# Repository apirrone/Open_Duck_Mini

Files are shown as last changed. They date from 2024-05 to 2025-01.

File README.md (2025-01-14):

# Open Duck Mini v2

Capture d’écran du 2025-01-14 15-44-05

I'm making a miniature version of the BDX Droid by Disney. It is about 42 centimeters tall with its legs extended.
The full BOM cost should be under $400 !

# This repo

This is kind of a hub where I centralize all resources related to this project. This is a working repo, so there are a lot of undocumented scripts :) I'll try to clean things up at some point.

# CAD

https://cad.onshape.com/documents/64074dfcfa379b37d8a47762/w/3650ab4221e215a4f65eb7fe/e/0505c262d882183a25049d05

See [this document](docs/prepare_robot.md) for getting from a onshape design to a simulated robot in MuJoCo

# RL stuff

We now use [AWD](https://github.com/rimim/AWD)

## Actuator identification 

We used Rhoban's [BAM](https://github.com/Rhoban/bam)

# BOM

> The BOM is not yet fully finalized, wait a bit before ordering stuff

https://docs.google.com/spreadsheets/d/1gq4iWWHEJVgAA_eemkTEsshXqrYlFxXAPwO515KpCJc/edit?usp=sharing

# Build Guide

## Print Guide

TODO

## Assembly Guide
TODO

TODO

# Embedded runtime

This repo contains the code to run the policies on the onboard computer (Raspberry pi zero 2w) https://github.com/apirrone/Open_Duck_Mini_Runtime

> Thanks a lot to HuggingFace and Pollen Robotics for sponsoring this project !

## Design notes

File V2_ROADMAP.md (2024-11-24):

# V2 ROADMAP

First make the placo walk work with foot sensors -> This validate the design, the motors are powerful enough and urdf is close to the real thing

## CAD

### Notes :
- Plan mounting holes for aesthetic stuff later ?
- Plan to hide the cables somehow
- Integrate feet contact sensors (switchs, not fsr I think)

### TODO
  - [] Full redesign using feetech motors.
    - [] Select the motors STS3215 or STS3250 ? 5v ? 12 v (if 12v, need to change electronics)
  - [] Export new URDF and MJCF

## Motors modeling

### TODO
- [] BAM motors identification
- [] BAM in Isaac Gym

## Electronics

### Notes

Check what they did for Zeroth https://docs.zeroth.bot/build/bom
Maybe use all their electronics ? It's cheap and powerful apparently. Talk with JX

## Software

### TODO
- [] Cleanup Open Duck mini repo
- [] Add documentation
- [] Integrate v2
- [] V2 in AWD

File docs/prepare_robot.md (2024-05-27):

# Preparing a robot for simulation in MuJoCo

## If you designed your robot in OnShape

### Make sure to design you robot according to onshape-to-robot constraints
https://onshape-to-robot.readthedocs.io/en/latest/design.html

The urdf will contain frames named `closing_<...>_1` and `closing_<...>_2` that you can use to close the loops in the mjcf file.

### Get get robot urdf from onshape

Run

```bash
$ onshape-to-robot robots/bd1/
```

#### (Optional) If you have closing loops, follow the instructions for handling them in the documentation of onshape-to-robotn then:

In `robot.urdf`, add : 
```xml
<robot name="...">
    <mujoco>
        <compiler fusestatic="false"/>
    </mujoco>
	...
</robot>
```

# Convert URDF to MJCF (MuJoCo)

## Get MuJoCo binaries

Download mujoco binaries somewhere https://github.com/google-deepmind/mujoco/releases

unpack and run

```bash
$ ./compile robot.urdf robot.xml
```

## In robot.xml, add actuators : 
Example : 
```xml
	<actuator>
		<position name="left_hip_yaw"    joint="left_hip_yaw"    inheritrange="1"/>
		<position name="left_hip_roll"   joint="left_hip_roll"   inheritrange="1"/>
		<position name="left_hip_pitch"  joint="left_hip_pitch"  inheritrange="1"/>
		<position name="left_knee"       joint="left_knee"       inheritrange="1"/>
		<position name="left_ankle"      joint="left_ankle"      inheritrange="1"/>
		<position name="right_hip_roll"  joint="right_hip_roll"  inheritrange="1"/>
		<position name="right_hip_yaw"   joint="right_hip_yaw"   inheritrange="1"/>
		<position name="right_hip_pitch" joint="right_hip_pitch" inheritrange="1"/>
		<position name="right_knee"      joint="right_knee"      inheritrange="1"/>
		<position name="right_ankle"     joint="right_ankle"     inheritrange="1"/>
		<position name="head_pitch1"     joint="head_pitch1"     inheritrange="1"/>
		<position name="head_pitch2"     joint="head_pitch2"     inheritrange="1"/>
		<position name="head_yaw"        joint="head_yaw"        inheritrange="1"/>
	</actuator>
```

## Add a freejoint 

encapsulate the body in a freejoint
```xml
<worldbody>
	<body>
		<freejoint />
		...
		...
	</body>
</worldbody>
```

## (Optional) Constrain closing loop

Add the following to the mjcf file
```xml
<equality>
    <connect body1="closing_<...>_1" body2="closing_<...>_2" anchor="x y z" />
</equality>
```

the x, y, z values can be found in the .urdf 

```xml
<joint name="closing_<...>_1_frame" type="fixed">
	<origin xyz="x y z" rpy="r p y" />
	...
</joint>
```

## Setup collision groups, damping and friction
/!\ remove actuatorfrcrange in joints
Put that inside the <mujoco> bracket
```xml
<mujoco>
  <default>
    <geom contype="1" conaffinity="1" solref=".004 1" />
    <joint damping="0.09" frictionloss="0.1"/>
    <position kp="10" forcerange="-5.0 5.0"/>
  </default>
	...
	...
</mujoco>
```

still need to add : 
- change frames to sites

## Visualize 

```bash
$ python3 -m mujoco.viewer --mjcf=<path>/scene.xml
```

or 

```bash
$ <path_to_mujoco_bin>/bin/simulate <path>/scene.xml
```

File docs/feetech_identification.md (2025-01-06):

$\theta_d^f$ : $\theta$ requested in firmware units

$\epsilon = \theta_d^f - \theta^f$

### Error in firmware units

> $\lambda$ is the duty cycle, aka the **PWM**

$\epsilon^f = \epsilon \frac{4096}{2\pi}$

> 12 bits

### Firmware duty cycle 

$\lambda^f = K_p \epsilon^f$

$\lambda = K_p K_g\epsilon$

$R = 2.5\Omega$

------

$\lambda = \epsilon K_p K_g$

$K_g = \frac{\lambda}{\epsilon K_p }$

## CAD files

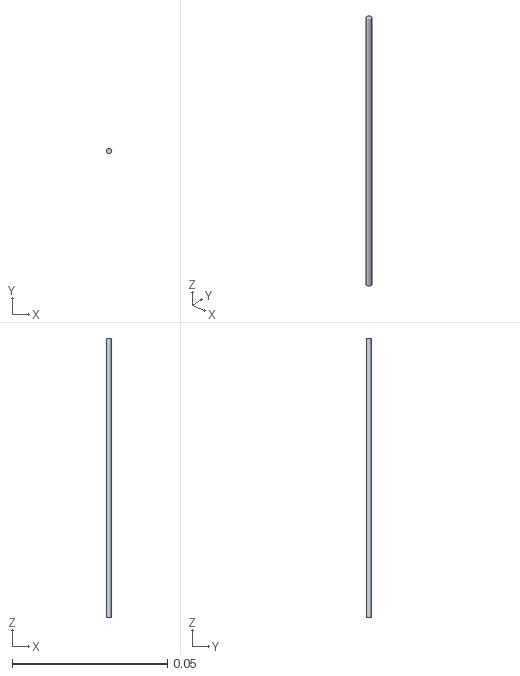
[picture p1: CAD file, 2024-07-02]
mini_bdx/robots/bdx/antenna.stl
0.00175 x 0.00175 x 0.09

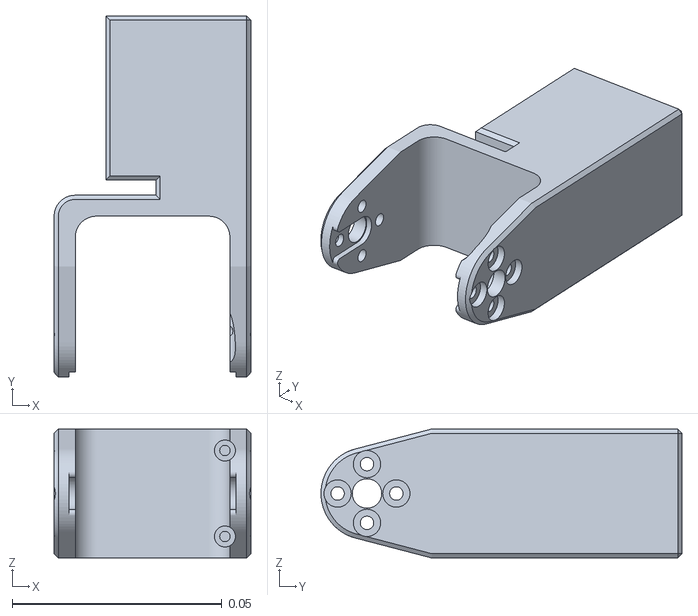
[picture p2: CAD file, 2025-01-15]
mini_bdx/robots/open_duck_mini_v2/left_roll_to_pitch.stl
0.0469 x 0.0861 x 0.0307

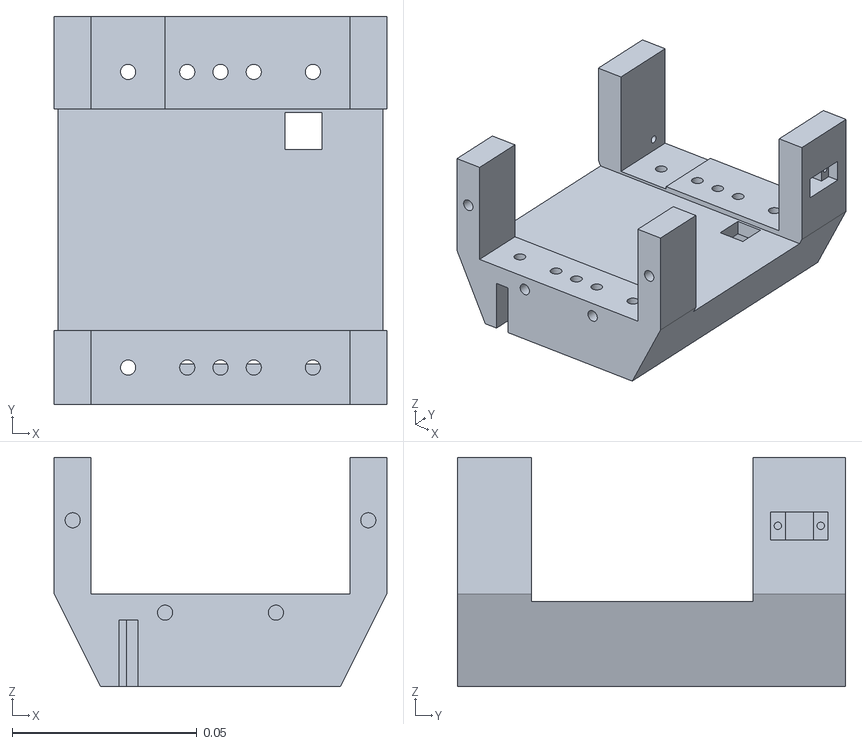
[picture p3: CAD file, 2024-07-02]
mini_bdx/robots/bdx/cage_bottom.stl
0.09 x 0.105 x 0.062

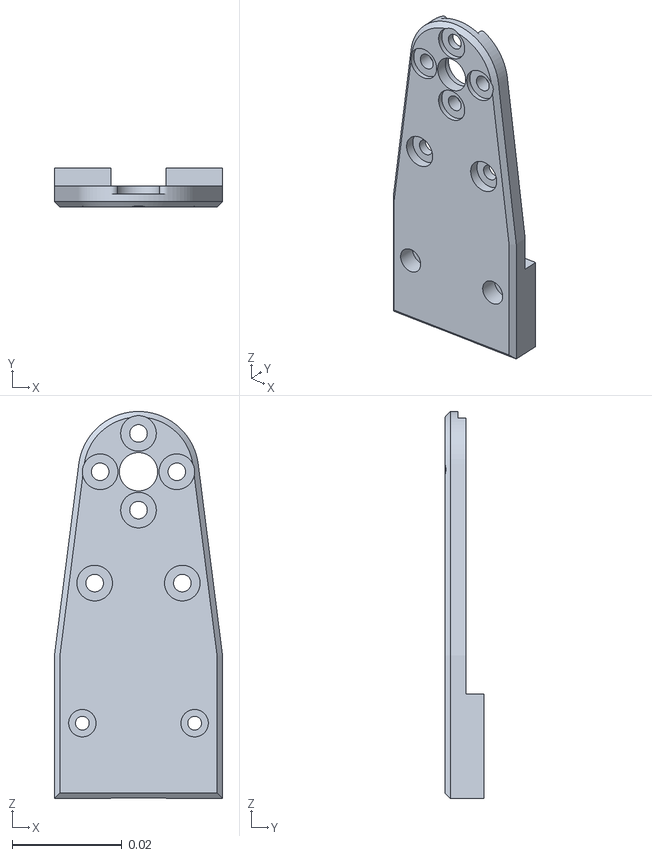
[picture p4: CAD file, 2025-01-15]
mini_bdx/robots/open_duck_mini_v2/left_knee_to_ankle_right_sheet.stl
0.0307 x 0.0072 x 0.0706

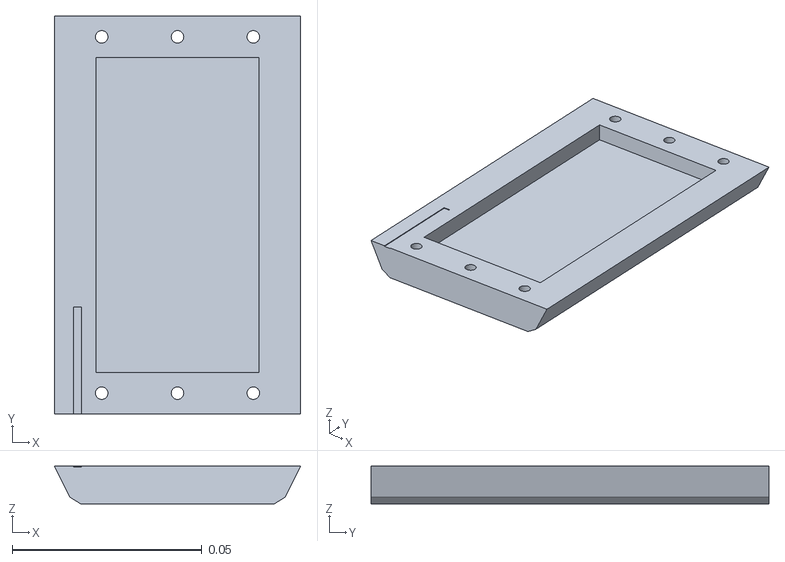
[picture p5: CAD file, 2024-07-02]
mini_bdx/robots/bdx/cage_bottom_battery_hold.stl
0.065 x 0.105 x 0.01

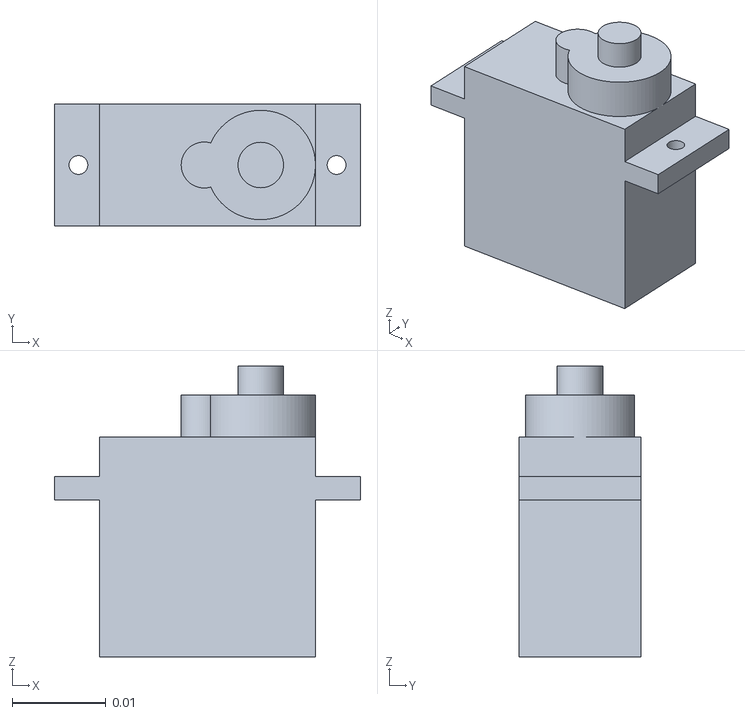
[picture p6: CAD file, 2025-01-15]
mini_bdx/robots/open_duck_mini_v2/sg90.stl
0.0326 x 0.013 x 0.031

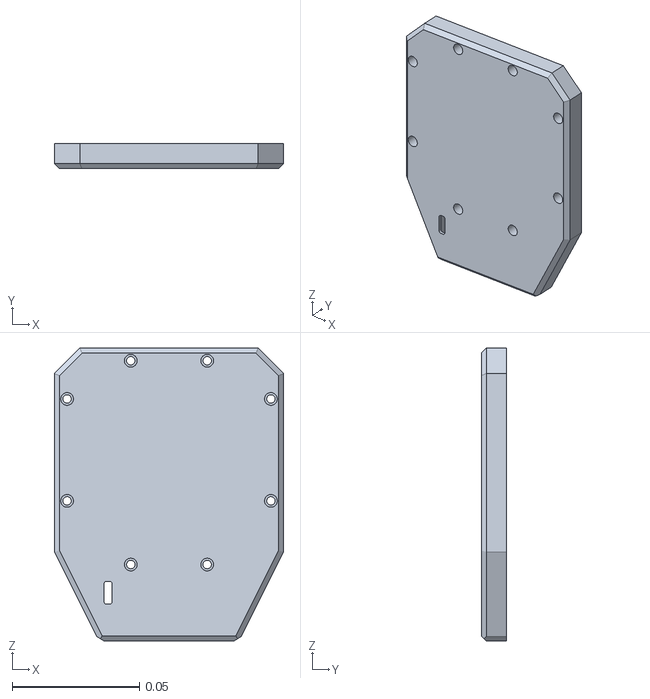
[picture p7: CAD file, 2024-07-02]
mini_bdx/robots/bdx/front_cover.stl
0.09 x 0.01 x 0.115

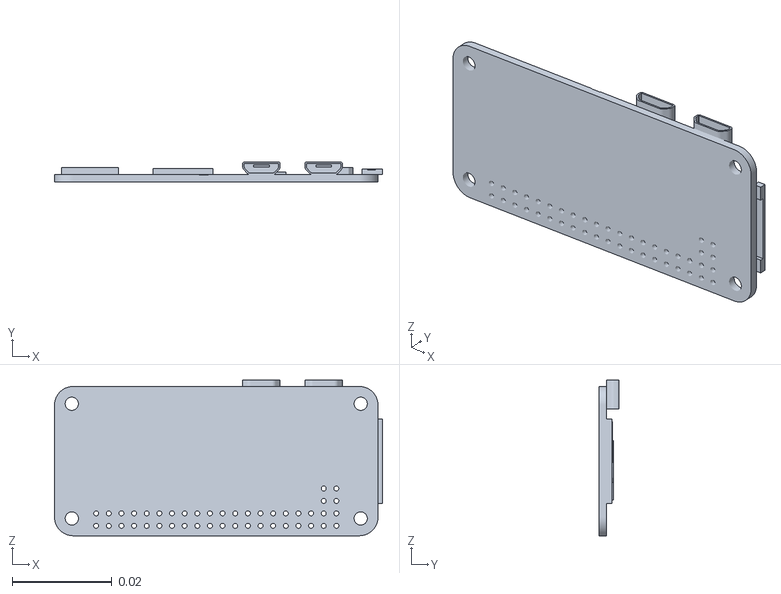
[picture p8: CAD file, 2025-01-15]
mini_bdx/robots/open_duck_mini_v2/raspberrypizerow.stl
0.0659 x 0.0041 x 0.0312

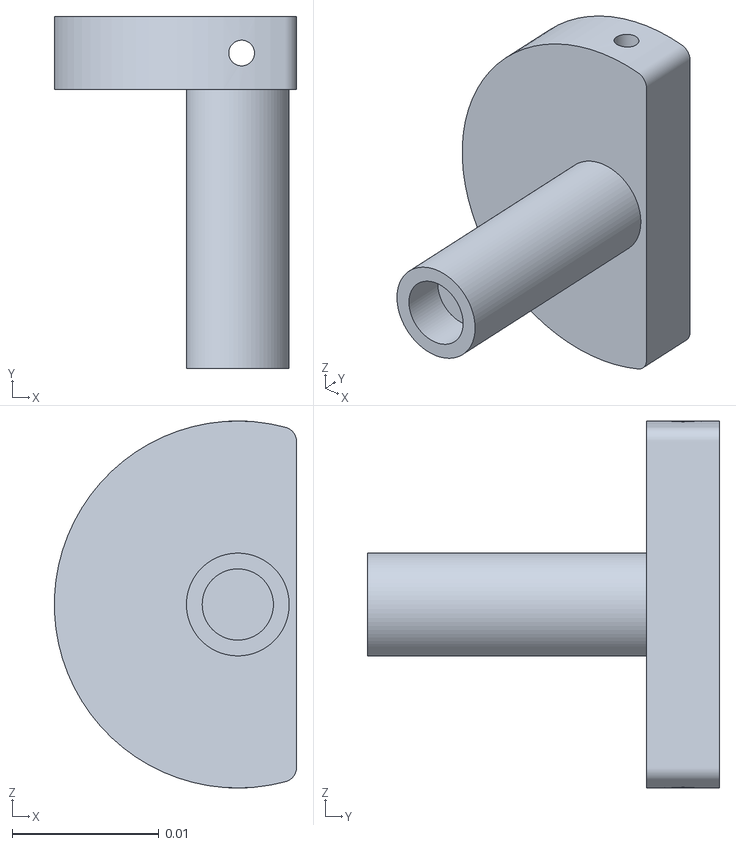
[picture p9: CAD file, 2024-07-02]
mini_bdx/robots/bdx/antenna_holder_right.stl
0.0165 x 0.024 x 0.025

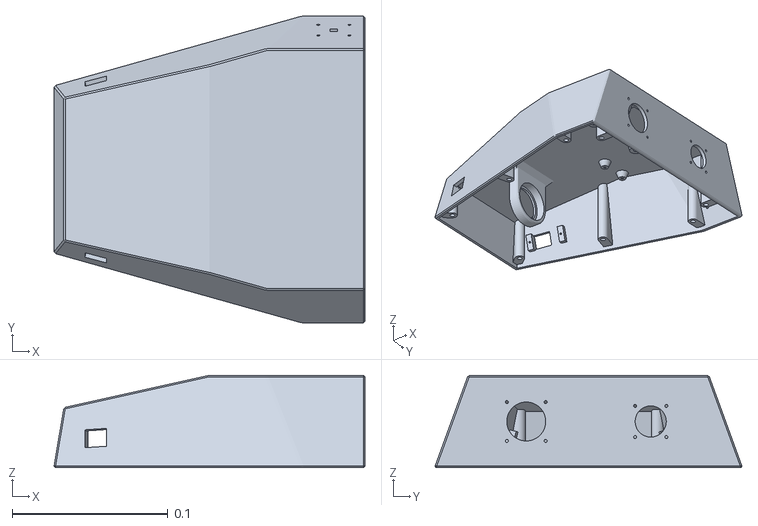
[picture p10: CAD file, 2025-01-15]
mini_bdx/robots/open_duck_mini_v2/head.stl
0.2 x 0.197 x 0.0594

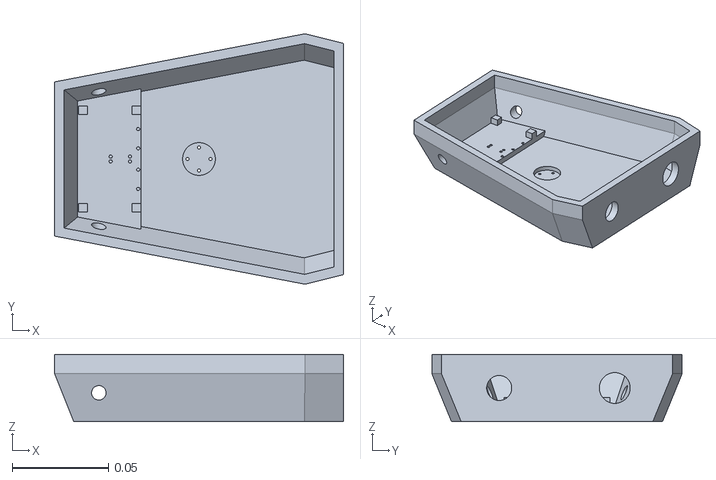
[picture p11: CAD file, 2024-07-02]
mini_bdx/robots/bdx/head.stl
0.15 x 0.13 x 0.035

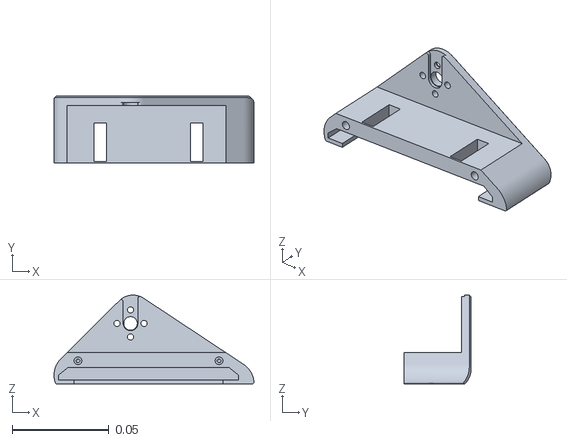
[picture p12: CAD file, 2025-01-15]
mini_bdx/robots/open_duck_mini_v2/foot_top.stl
0.103 x 0.0349 x 0.046

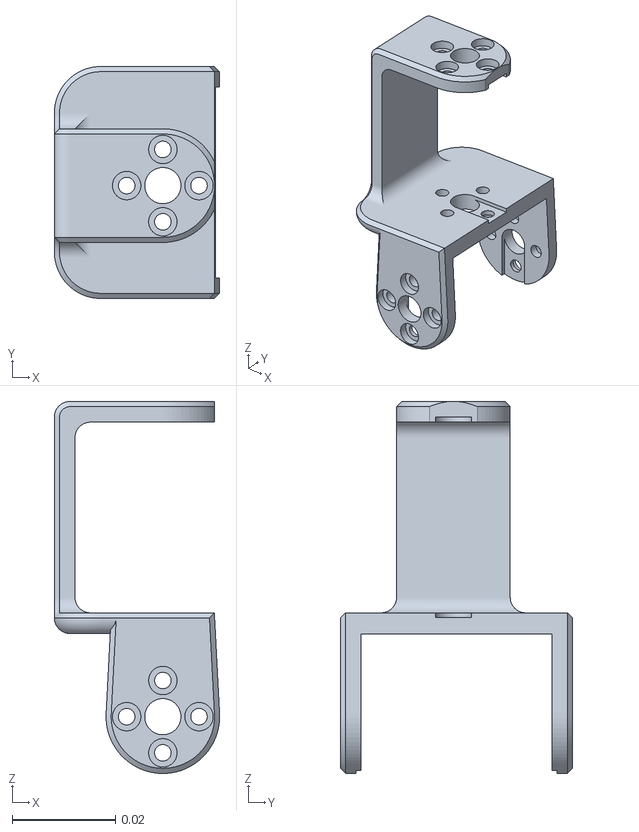
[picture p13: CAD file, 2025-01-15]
mini_bdx/robots/open_duck_mini_v2/head_pitch_to_yaw.stl
0.032 x 0.0449 x 0.072

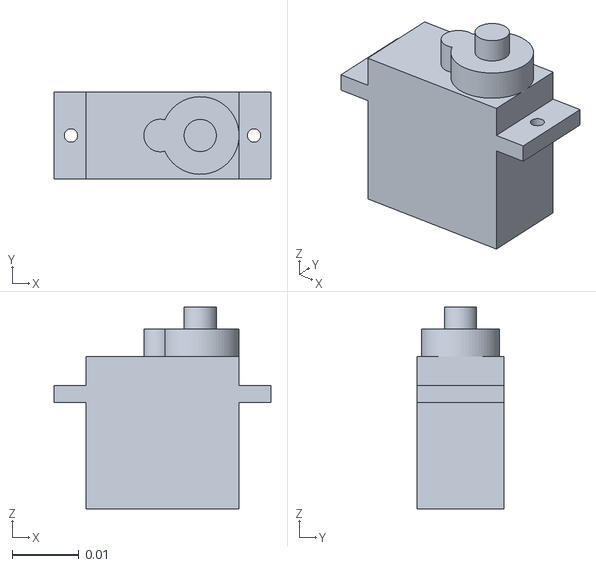
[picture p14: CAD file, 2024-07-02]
mini_bdx/robots/bdx/sg90.stl
0.0326 x 0.013 x 0.0303

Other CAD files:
mini_bdx/robots/bdx/antenna_holder_left.stl
mini_bdx/robots/open_duck_mini_v2/left_knee_to_ankle_left_sheet.stl
mini_bdx/robots/bdx/antenna_tip.stl
mini_bdx/robots/open_duck_mini_v2/trunk_top.stl
mini_bdx/robots/bdx/39281023.prt.stl
mini_bdx/robots/bdx/antenna_motor_holder.stl
mini_bdx/robots/bdx/axis_to_axis.stl
mini_bdx/robots/bdx/block_to_axis.stl
mini_bdx/robots/bdx/board.stl
mini_bdx/robots/bdx/body_part.stl
mini_bdx/robots/bdx/cage_back.stl
mini_bdx/robots/bdx/cage_top.stl
mini_bdx/robots/bdx/dc15_a01_case_b_dummy.stl
mini_bdx/robots/bdx/dc15_a01_case_f_dummy.stl
mini_bdx/robots/bdx/dc15_a01_case_m_dummy.stl
mini_bdx/robots/bdx/dc15_a01_horn_dummy.stl
mini_bdx/robots/bdx/dc15_a01_horn_idle2_dummy.stl
mini_bdx/robots/bdx/double_u.stl
mini_bdx/robots/bdx/foot.stl
mini_bdx/robots/bdx/foot_contact.stl
mini_bdx/robots/bdx/head_roll_pitch.stl
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

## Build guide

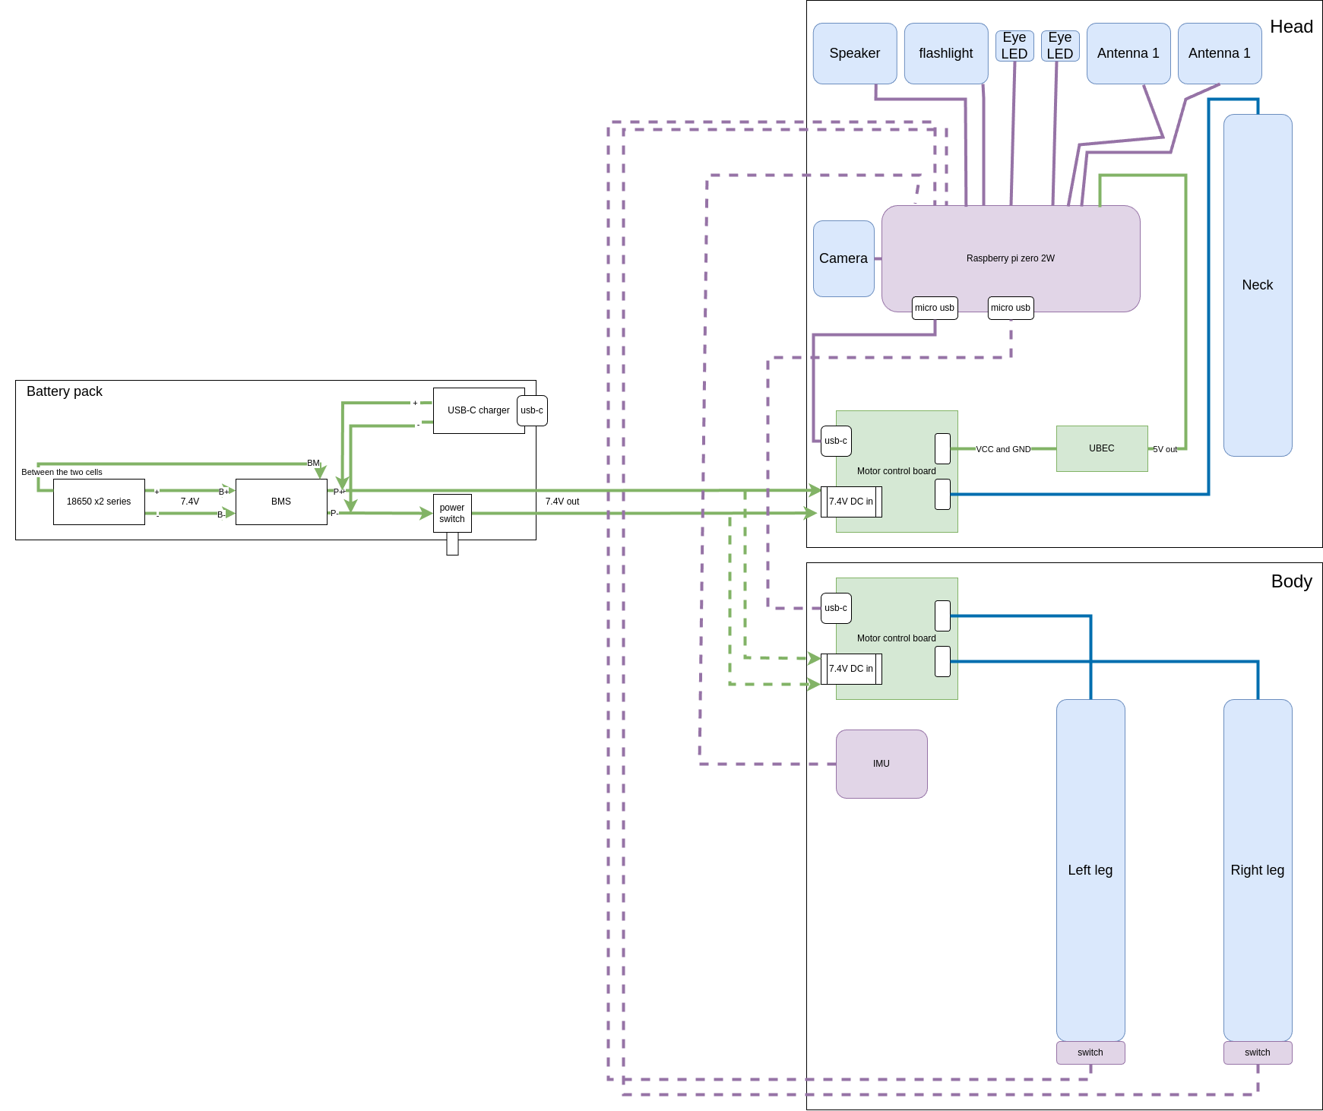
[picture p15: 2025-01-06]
docs/open_duck_mini_v2_wiring_diagram.png

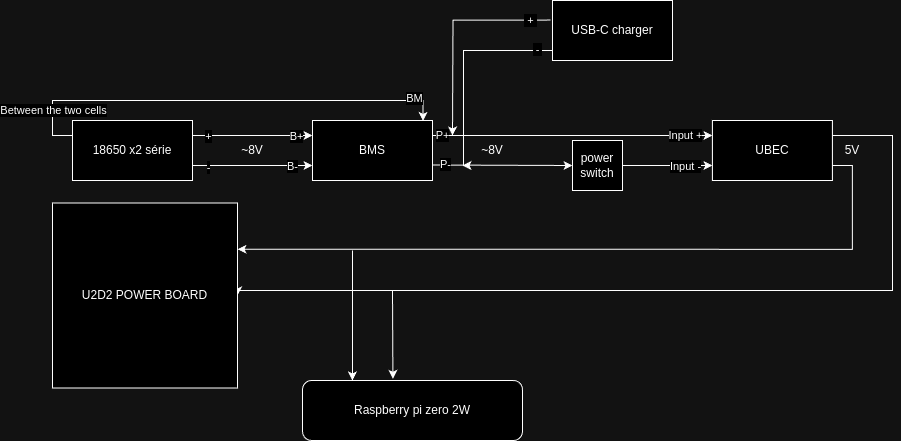
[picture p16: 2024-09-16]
docs/open_duck_mini_v1_wiring_diagram.png

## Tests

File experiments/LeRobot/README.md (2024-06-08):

# Current state of things

Tried to clean up `record_episodes_hdf5.py` by using `bdx_mujoco_server.py` but got weird behavior with the walk engine.

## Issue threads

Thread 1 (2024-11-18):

Clarification on UBEC Assembly in Body Module

lixinyao11, 2024-11-18:
Hi there,

Thank you for sharing this fantastic project! I’ve been working on building a robot following your design on Onshape. However, I noticed that the UBEC part is not included in the body module, even though it is listed in the BOM and Parts tab. Additionally, based on your wiring diagram, the UBEC seems to be a necessary component for the body assembly.

Could you kindly advise on how to assemble the UBEC in the body module? Alternatively, if possible, could the Onshape page be updated to include this information?

Thank you for your time and assistance! I really appreciate your efforts in making this project accessible.

apirrone, 2024-11-18:
Hi!

Yeah, the UBEC module is just stuffed in the back of the robot, there is space in the cavity below the u2d2 power board. It's not great design 😅

I should add this in the readme, but I would advise waiting (a few months probably) for the v2 version instead of building the current version. We'll start the design soon, it should be cheaper, better designed and easier to build (with better docs too). If you already started building the current version, I'll help you make things work of course !

Thanks !

lixinyao11, 2024-11-21:
Hi!

Thank you for your help! I have already started building the current version and I will try to make things work! Also looking forward to your v2 version! : )

Closed 2024-11-21.

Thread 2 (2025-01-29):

Isaac sim environment

benoit-robotics, 2025-01-29:
Hello,
In case you're interested, I created an Isaac sim environment to train your robot to walk : https://github.com/benoit-robotics/bdx_walk_rl .
It's for the v1 but it should be very easy to modify it to train v2 instead.
Cheers

apirrone, 2025-02-06:
Nice ! I'll look into that :) The video on your readme seems broken though

benoit-robotics, 2025-02-07:
Thank you for letting me know, I updated the link to the video

Closed 2025-04-06.

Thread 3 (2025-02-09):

The bolt size is incorrect in the Assembly Instructions.

SX-GitHub, 2025-02-09:
"Then assamble trunk_bottom and trunk_top, and screw them together with 2 M3x6 screws through these holes", the bolts need to be M3x10.

apirrone, 2025-02-09:
Ah yes thanks, I'll change that !

apirrone, 2025-02-09:
Done ! I'm keeping the issue open if you have more remarks during your build :) Thanks !

apirrone, 2025-02-11:
Yes, for now I use the LeRobot configure script (from https://github.com/huggingface/lerobot) like this

```bash
python lerobot/scripts/configure_motor.py \                                                                                                                                              
                                               --port /dev/ttyACM0 \
                                               --brand feetech \
                                               --model sts3215 \
                                               --baudrate 1000000 \
                                               --ID 1
```

(Change the id for each motor according to this https://github.com/apirrone/Open_Duck_Mini_Runtime/blob/0c5d84742d18f482ba59199c960755cd2842e6f1/mini_bdx_runtime/mini_bdx_runtime/hwi_feetech_pwm_control.py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)

The motor will move to the 180 position during configuration, which is the actual zero position we want.

I'll add scripts and documentation to do this soon !

Closed 2025-03-20.

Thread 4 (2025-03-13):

Beee pooo beee - Great project!

SourceCipher, 2025-03-13:
I have been looking everywhere if anyone actually made something like this and its amazing to find so much work released for free!
Do you guys have any discord or youtube channels where people can stay in contact and ask questions as with github its a bit difficult I guess 🤖

**Thanks for this project!**

boom567, 2025-03-14:
Good ideal ! I'm waiting for it too. Now I am printing the shell !

SourceCipher, 2025-03-14:
Yeah I havent started on any of it as I currently dont have access to my 3d printer, but I am more interesting in the actual AI training to make this robot walk like the disneys one does. Ofc I doubt its even possible without using some expensive actuators, but it would be cool to understand it all how the whole reinforcement learning works and can be adopted to the real world robots as from what I searched there are really small amount of videos or sources of how to apply this.

apirrone, 2025-03-15:
We just opened a public section of our discord, feel free to join and ask your questions here ! https://discord.gg/UtJZsgfQGe

Closed 2025-03-20.

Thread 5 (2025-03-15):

servo  compatibility

geppetto32, 2025-03-15:
Hello ..
your project is really good and interesting .
I want to try it ou and build it but I have a question about the servos which is if the waveshare ST3215 is compatible with the servo library you use.
it will be a huge relief if are compatible because it happens to have all the needed servos.

https://www.waveshare.com/wiki/ST3215_Servo

Thank you and excuse my English .

geppetto32, 2025-03-16:
Good morning , thats great ... i have some HS that i wll use them on legs and the ST3215's for the neck. I have already started printing , soon i will have some results.
Thank you..

Closed 2025-03-20.

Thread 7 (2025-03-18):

The holes (two) on RIGHT_ROLL_TO_PITCH/LEFT_ROLL_TO_PITCH are not concentric with the holes on the servos

TonyInvent, 2025-03-18:
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
RIGHT_ROLL_TO_PITCH, LEFT_ROLL_TO_PITCH

The holes (two) on RIGHT_ROLL_TO_PITCH/LEFT_ROLL_TO_PITCH are not concentric with the holes on the servos. 1.18 mm misaligned.

apirrone, 2025-03-18:
You're right, nice catch! It's fixed in the CAD now, I'll update the stl files in the repo.

before

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

after

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

Thanks !

Closed 2025-03-19.

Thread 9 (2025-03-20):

About the BOM

parkerpanjs, 2025-03-20:
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
 Is there a little mistake?
these two items are the same electric board.

apirrone, 2025-03-20:
Indeed, just fixed it. Thanks !

parkerpanjs, 2025-03-21:
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   and the bom do not include the camera, so what is it?

Closed 2025-03-20.

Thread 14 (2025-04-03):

Confused about the ss10 switch

maowenniao, 2025-04-03:
Hello~
I noticed there are two SS10 should be mounted on the bottom of the feet. But I can't find any information about how to install them. Could you show us the picture of the switch after installation? Many thanks.

apirrone, 2025-04-03:
Yeah sorry it's not documented, I'll add it today. You just have to press them in their holes such that the switch is activated when the foot touches the ground

Closed 2025-04-03.

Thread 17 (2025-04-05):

3d print part issue

maowenniao, 2025-04-05:
hello apirrone, it's me again.
I am trying to assemble this cute Duck, and I found a little bite of conflict when I try to assemble the "roll to pitch" and "roll motor bottom".
There is a mount screw should be mounted on the "roll motor bottom", after the screw has been mounted, the screw head will protrude and push against the "roll to pitch",and hindering its movement.
I suggest making a slot for the screw on the "roll to pitch" to avoid the position of this conflict.
Many thanks!

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

apirrone, 2025-04-06:
Hi @maowenniao, thanks for the feedback!
I'm aware of this, we need to dig a slot on the hip_to_pitch part so that this screw can pass better.
On my duck, it ended up digging its own slot so it's not a very big deal, but it would be cleaner for sure !

maowenniao, 2025-04-06:
Many thanks!!!
And the last question, what's the zero position for the motors? When I produce the "motor offset" process, I am confusing about the original posture o the Duck.
Picture 1 :
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

Picture 2:
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

Which one is the right position for setting "Motors offset"?

Many thanks!!!!

apirrone, 2025-04-07:
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

This is the zero position of the duck. When sending 0 to all motors, it should be in this position. The `find_soft_offsets.py` script will set the robot to this zero position and let you find small offsets to compensate small inaccuracies when mounting the robot. If when running the `find_soft_offsets.py` script your robot goes to the position on picture 2, something is wrong, you have mounted some servos with the wrong orientation.

When running the `configure_motor.py` script, it will move the servo to its zero position fyi

maowenniao, 2025-04-07:
Thanks a lot. I am using the 12V servo and using the 12V 3S battery.

I will update you on some optimization if my duck running well.
Many thanks!

maowenniao, 2025-04-12:
Hello, I just want to check if there is any chance that you will share the raw design drawings of the 3D part? We want to do many adjustment to fit raspberry pi 5，ss1603 screen, 3S power battery and more sensors?
Many thanks!

apirrone, 2025-04-12:
All the design is in onshape (linked in the readme )
 https://cad.onshape.com/documents/64074dfcfa379b37d8a47762/w/3650ab4221e215a4f65eb7fe/e/0505c262d882183a25049d05

You can freely fork the document to edit it, or export the parts in .step to modify them in the cad software you like

Closed 2025-04-07.

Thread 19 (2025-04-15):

Improve documentation

apirrone, 2025-04-15:
Fix the todos, outdated pictures and info

Also, add a FAQ section with Q/A from the community

maowenniao, 2025-04-19:
I made a adapter PCB for the zero w2 and raspberry pi4 for this project.
Do you need this?

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

Rpi4

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

blublear, 2025-04-20:
I also made an adapter board that uses standard 2.54mm pin headers. @maowenniao what is the connector and pitch on your board?

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

maowenniao, 2025-04-26:
> I also made an adapter board that uses standard 2.54mm pin headers. @maowenniao what is the connector and pitch on your board?
>
> 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

Xh2.54

maowenniao, 2025-04-26:
> That's super cool!! I really have to try that !

I will sent you the shared link

maowenniao, 2025-04-26:
> That's super cool!! I really have to try that !

https://github.com/[maowenniao/Duck-mini-adapter](https://github.com/maowenniao/Duck-mini-adapter)

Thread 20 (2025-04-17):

motor kp and kd

kassasin, 2025-04-17:
Hello, recently I am doing sim2real for my robot. I noticed in mjcf ,motor kp and kd is 17.8 and 0, should modify them in servo motor's software ?

apirrone, 2025-04-17:
Hi, the 17.8 in mujoco corresponds to 32 in the motors firmware units

kassasin, 2025-04-18:
> Hi, the 17.8 in mujoco corresponds to 32 in the motors firmware units

Thanks，understand！

Closed 2025-04-18.

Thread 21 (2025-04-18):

Other motor adaptation issues

edyang, 2025-04-18:
Thank you, bro

I used a 12v, 30kg STS3215, and after running the command

`python v2_rl_walk_maujoco. py -- onnx_mod. path~/BEST_WALK_ONNX2. onnx - p 32-- commands -- cutoff_frequency 40`

 my feet kept trembling. What do I need to adjust?

edyang, 2025-04-18:
Additional explanation: Compared to the 7.4v servo, the manufacturer claims that this 12v servo can also be driven normally at 7.4v, and the gear ratio of the servo is the same. I can also set it to the specified angle when using it normally

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

apirrone, 2025-04-19:
> the manufacturer claims that this 12v servo can also be driven normally at 7.4v, and the gear ratio of the servo is the same

Can you share where you find that information ?

Right now we believe that the 12v servos and the 7.4v ones are different, meaning they require different parameters to be simulated (parameters given by system identification) so it's not surprising to me that using `BEST_WALK_ONNX2.onnx` doesn't work with your 12v servos since it was trained for 7.4v servos.

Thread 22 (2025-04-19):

Add missing stl files

apirrone, 2025-04-19:

apirrone, 2025-04-19:
Done by https://github.com/apirrone/Open_Duck_Mini/commit/730c14bc50e4e60c4a983f57fd739e015510cc76

Closed 2025-04-19.

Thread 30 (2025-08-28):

The duck cannot be lifted up and retreated by the handle

K-Shuffler, 2025-08-28:
This is an excellent open-source project that has taught me a great deal.
However, I've encountered a peculiar issue: when controlling the duck with an Xbox controller, it doesn't walk as expected—it seems to lack a proper gait.
Could this be caused by the servo movement direction for the duck's legs not being mirrored?

apirrone, 2025-08-28:
Hi! I would suggest joining the discord server to ask your question there, it'll be easier to help you debug this !

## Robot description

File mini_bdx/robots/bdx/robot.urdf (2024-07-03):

<robot name="onshape">
    <mujoco>
        <compiler fusestatic="false"/>
    </mujoco>
    <link name="body_module">
        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
        <inertial>
            <origin xyz="-0.00675679511969270747 -0.006637466546945220737 0.0078705246973564610413" rpy="0 0 0"/>
            <mass value="0.50186117579999178773" />
            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
        </inertial>
    </link>
    <link name="trunk">
        <inertial>
            <origin xyz="0 0 0" rpy="0 0 0" />
            <mass value="1e-9" />
            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
        </inertial>
    </link>
    <joint name="trunk_frame" type="fixed">
        <origin xyz="0.032527100485028298538 -0.0066038964305764145252 0.012578922950962011587" rpy="1.5111348801390835856e-14 -6.2433989600656048221e-14 9.1593399531630240418e-16" />
        <parent link="body_module" />
        <child link="trunk" />
        <axis xyz="0 0 0"/>
    </joint>
    <link name="double_u_module">
        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
        <inertial>
            <origin xyz="-0.017000000000027194746 -8.4248510725113835815e-05 0.01158451252812944636" rpy="0 0 0"/>
            <mass value="0.018818301231819770797" />
            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
        </inertial>
    </link>
    <link name="right_hip_pitch_roll_module">
        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
        <inertial>
            <origin xyz="0.011912825164996051694 -0.011752076745460894591 -0.0064503420228230780309" rpy="0 0 0"/>
            <mass value="0.050685765935093662904" />
            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
        </inertial>
    </link>
    <link name="leg_module">
        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
        <inertial>
            <origin xyz="-0.039901628351739881762 -7.7113301695330656099e-06 0.011400440323216621402" rpy="0 0 0"/>
            <mass value="0.034530807353386039349" />
            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
        </inertial>
    </link>
    <link name="leg_module_2">
        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
        <inertial>
            <origin xyz="-0.039901628351740887901 -7.7113301699271358301e-06 0.011400440323216496502" rpy="0 0 0"/>
            <mass value="0.034530807353386039349" />
            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
        </inertial>
    </link>
    <link name="foot_module">
        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
        <inertial>
            <origin xyz="-0.026873167661377921067 0.0076028406460558663887 0.011556240850102265233" rpy="0 0 0"/>
            <mass value="0.028234070013912770242" />
            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
        </inertial>
    </link>
    <link name="right_foot">
        <inertial>
            <origin xyz="0 0 0" rpy="0 0 0" />
            <mass value="1e-9" />
            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
        </inertial>
    </link>
    <joint name="right_foot_frame" type="fixed">
        <origin xyz="-0.037499999999999034106 -6.6570013390609972248e-17 0.011499999999999982458" rpy="1.5707963267948954478 -9.9920072216265019494e-15 1.570796326794896558" />
        <parent link="foot_module" />
        <child link="right_foot" />
        <axis xyz="0 0 0"/>
    </joint>
    <joint name="right_ankle" type="revolute">
        <origin xyz="-0.065000000000002070011 -9.0726037793587011038e-16 1.249000902703301108e-16" rpy="-1.028864493624538396e-14 7.7715611723731079723e-16 2.0438598593485175549e-14" />
        <parent link="leg_module_2" />
        <child link="foot_module" />
        <axis xyz="0 0 1"/>
        <limit effort="1" velocity="20" lower="-1.570796326794896558" upper="1.570796326794896558"/>
        <joint_properties friction="0.0"/>
    </joint>
    <joint name="right_knee" type="revolute">
        <origin xyz="-0.065000000000000890399 -1.8409752888803865289e-16 2.3592239273284576484e-16" rpy="1.1102230529243367767e-16 2.2204460492507932999e-16 -1.1500818382616808057e-13" />
        <parent link="leg_module" />
        <child link="leg_module_2" />
        <axis xyz="0 0 1"/>
        <limit effort="1" velocity="20" lower="-2.0943951023931952626" upper="2.0943951023931952626"/>
        <joint_properties friction="0.0"/>
    </joint>
    <joint name="right_hip_pitch" type="revolute">
        <origin xyz="0.025000000000000646705 -0.024500000000000743405 -0.013499999999999783007" rpy="1.5707963267948972241 -9.4876329561990965088e-14 -3.141592653589793116" />
        <parent link="right_hip_pitch_roll_module" />
        <child link="leg_module" />
        <axis xyz="0 0 1"/>
        <limit effort="1" velocity="20" lower="-0.52359877559829881566" upper="1.570796326794896558"/>
        <joint_properties friction="0.0"/>
    </joint>
    <joint name="right_hip_roll" type="revolute">
        <origin xyz="-0.033999999999999905298 0.011499999999999989397 0.011499999999999895722" rpy="-1.5707963267948958919 -1.570796326794896336 0" />
        <parent link="double_u_module" />
        <child link="right_hip_pitch_roll_module" />
        <axis xyz="0 0 1"/>
        <limit effort="1" velocity="20" lower="-1.570796326794896558" upper="0.43633231299858238339"/>
        <joint_properties friction="0.0"/>
    </joint>
    <joint name="right_hip_yaw" type="revolute">
        <origin xyz="0.00012710048502765305023 -0.031603896430576608467 0.023078922950959548932" rpy="3.1415926535897304994 -1.5078389055347532112e-14 1.5707963267948974462" />
        <parent link="body_module" />
        <child link="double_u_module" />
        <axis xyz="0 0 1"/>
        <limit effort="1" velocity="20" lower="-0.69813170079773179122" upper="0.69813170079773179122"/>
        <joint_properties friction="0.0"/>
    </joint>
    <link name="double_u_module_2">
        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
        <inertial>
            <origin xyz="0.016999999999973376685 8.4512528129653690951e-05 0.011584248510725111622" rpy="0 0 0"/>
            <mass value="0.018818301231819770797" />
            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
        </inertial>
    </link>
    <link name="left_hip_pitch_roll_module">
        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
        <inertial>
            <origin xyz="0.011923026842605558007 -0.011606470860263534695 -0.016315085728328005549" rpy="0 0 0"/>
            <mass value="0.050936078435093665173" />
            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
        </inertial>
    </link>
    <link name="leg_module_3">
        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
        <inertial>
            <origin xyz="-0.039901628351738722966 -7.7113301693715381209e-06 0.011400440323216406296" rpy="0 0 0"/>
            <mass value="0.034530807353386039349" />
            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
        </inertial>
    </link>
    <link name="leg_module_4">
        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
        <inertial>
            <origin xyz="-0.039901628351739659717 -7.7113301683934352954e-06 0.011400440323216956204" rpy="0 0 0"/>
            <mass value="0.034530807353386039349" />
            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
        </inertial>
    </link>
    <link name="foot_module_2">
        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
        <inertial>
            <origin xyz="-0.026873167661378146581 0.0076028406460558776644 0.011556240850102180232" rpy="0 0 0"/>
            <mass value="0.028234070013912770242" />
            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
        </inertial>
    </link>
    <link name="left_foot">
        <inertial>
            <origin xyz="0 0 0" rpy="0 0 0" />
            <mass value="1e-9" />
            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
        </inertial>
    </link>
    <joint name="left_foot_frame" type="fixed">
        <origin xyz="-0.037499999999999256151 -5.2475385148298414606e-17 0.011499999999999850619" rpy="1.5707963267948954478 -9.9737163921664587049e-15 1.570796326794896558" />
        <parent link="foot_module_2" />
        <child link="left_foot" />
        <axis xyz="0 0 0"/>
    </joint>
    <joint name="left_ankle" type="revolute">
        <origin xyz="-0.065000000000000140998 1.6111244283134595889e-15 8.7430063189231077558e-16" rpy="-1.1368826724137153788e-14 1.6596211705633574847e-14 -2.1322488822902390562e-14" />
        <parent link="leg_module_4" />
        <child link="foot_module_2" />
        <axis xyz="0 0 1"/>
        <limit effort="1" velocity="20" lower="-1.570796326794896558" upper="1.570796326794896558"/>
        <joint_properties friction="0.0"/>
    </joint>
    <joint name="left_knee" type="revolute">
        <origin xyz="-0.064999999999998281375 -5.8763757748714340323e-17 0" rpy="5.970893051203023059e-16 -1.4853578868213746426e-14 -7.8207310266750229308e-08" />
        <parent link="leg_module_3" />
        <child link="leg_module_4" />
        <axis xyz="0 0 1"/>
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

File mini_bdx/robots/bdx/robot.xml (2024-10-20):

<mujoco model="bdx">
  <compiler angle="radian"/>
  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
  <default>
    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

    <joint damping="0.095" frictionloss="0.058" armature="0.0018"/>
    <position kp="2.54" kv="0.0" forcerange="-0.8 0.8"/>
    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

  </default>
  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
  <worldbody>
    <body name="base" pos="0 0 0.17">
    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
      <freejoint />
      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
      <body name="body_module">
        <inertial pos="-0.0067568 -0.00663747 0.00787052" quat="0.424416 0.567509 0.572577 0.412263" mass="0.501861" diaginertia="0.00136049 0.00104215 0.000854271"/>
        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
        <body name="trunk" pos="0.0325271 -0.0066039 0.0125789" quat="1 0 0 0">
          <inertial pos="0 0 0" mass="1e-09" diaginertia="0 0 0"/>
        </body>
        <body name="double_u_module" pos="0.0001271 -0.0316039 0.0230789" quat="0 0.707107 0.707107 0">
          <inertial pos="-0.017 -8.42485e-05 0.0115845" quat="0.259261 0.625097 0.282096 0.680043" mass="0.0188183" diaginertia="4.61959e-06 4.61664e-06 4.1639e-06"/>
          <joint name="right_hip_yaw" pos="0 0 0" axis="0 0 1" range="-0.698132 0.698132" />
          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
          <body name="right_hip_pitch_roll_module" pos="-0.034 0.0115 0.0115" quat="0.5 -0.5 -0.5 -0.5">
            <inertial pos="0.0119128 -0.0117521 -0.00645034" quat="0.664115 0.369051 0.335976 0.556662" mass="0.0506858" diaginertia="1.56781e-05 1.47443e-05 8.52074e-06"/>
            <joint name="right_hip_roll" pos="0 0 0" axis="0 0 1" range="-1.5708 0.436332" />
            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
            <body name="leg_module" pos="0.025 -0.0245 -0.0135" quat="0 0 -0.707107 -0.707107">
              <inertial pos="-0.0399016 -7.71133e-06 0.0114004" quat="0.502878 0.497012 0.497197 0.50288" mass="0.0345308" diaginertia="2.06535e-05 1.77761e-05 5.01407e-06"/>
              <joint name="right_hip_pitch" pos="0 0 0" axis="0 0 1" range="-0.523599 1.5708" />
              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
              <body name="leg_module_2" pos="-0.065 0 0" quat="1 0 0 0">
                <inertial pos="-0.0399016 -7.71133e-06 0.0114004" quat="0.502878 0.497012 0.497197 0.50288" mass="0.0345308" diaginertia="2.06535e-05 1.77761e-05 5.01407e-06"/>
                <joint name="right_knee" pos="0 0 0" axis="0 0 1" range="-2.0944 2.0944" />
                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
                <body name="foot_module" pos="-0.065 0 0" quat="1 0 0 0">
                  <inertial pos="-0.0268732 0.00760284 0.0115562" quat="0.443056 0.532696 -0.463707 0.552189" mass="0.0282341" diaginertia="1.31872e-05 1.21932e-05 5.15725e-06"/>
                  <joint name="right_ankle" pos="0 0 0" axis="0 0 1" range="-1.5708 1.5708" />
                  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
                  <body name="right_foot" pos="-0.0375 0 0.0115" quat="0.5 0.5 0.5 0.5">
                    <inertial pos="0 0 0" mass="1e-09" diaginertia="0 0 0"/>
                  </body>
                </body>
              </body>
            </body>
          </body>
        </body>
        <body name="double_u_module_2" pos="0.0001271 0.0183961 0.0230789" quat="0 0.707107 0.707107 0">
          <inertial pos="0.017 8.45125e-05 0.0115842" quat="-0.281391 0.680335 -0.258685 0.625336" mass="0.0188183" diaginertia="4.61959e-06 4.61664e-06 4.1639e-06"/>
          <joint name="left_hip_yaw" pos="0 0 0" axis="0 0 1" range="-0.698132 0.698132" />
          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
          <body name="left_hip_pitch_roll_module" pos="0.034 -0.0115 0.0115" quat="0.5 0.5 -0.5 0.5">
            <inertial pos="0.011923 -0.0116065 -0.0163151" quat="0.367078 0.649645 0.581274 0.324555" mass="0.0509361" diaginertia="1.57911e-05 1.48967e-05 8.554e-06"/>
            <joint name="left_hip_roll" pos="0 0 0" axis="0 0 1" range="-1.5708 0.436332" />
            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
            <body name="leg_module_3" pos="0.025 -0.0015 -0.0095" quat="2.76505e-08 2.76505e-08 0.707107 -0.707107">
              <inertial pos="-0.0399016 -7.71133e-06 0.0114004" quat="0.502878 0.497012 0.497197 0.50288" mass="0.0345308" diaginertia="2.06535e-05 1.77761e-05 5.01407e-06"/>
              <joint name="left_hip_pitch" pos="0 0 0" axis="0 0 1" range="-0.523599 1.5708" />
              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

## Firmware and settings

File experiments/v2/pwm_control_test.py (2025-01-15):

from pypot.feetech import FeetechSTS3215IO
import time
import numpy as np
from threading import Thread
import pickle


io = FeetechSTS3215IO(
    "/dev/ttyACM0",
    baudrate=1000000,
    use_sync_read=True,
)
# io.disable_torque([1])
# input()
# io.enable_torque([1])
# input()
# io.disable_torque([1])
# exit()

class FeetechPWMControl:
    def __init__(self):
        self.io = FeetechSTS3215IO(
            "/dev/ttyACM0",
            baudrate=1000000,
            use_sync_read=True,
        )
        self.id = 1

        # TODO zero first
        self.io.enable_torque([self.id])
        self.io.set_mode({self.id: 0})
        self.io.set_goal_position({self.id: 0})
        time.sleep(1)
        # exit()

        self.io.set_mode({self.id: 2})
        self.kp = self.io.get_P_coefficient([self.id])[0]

        self.control_freq = 100  # Hz
        self.goal_position = 0
        self.present_position = 0
        Thread(target=self.update, daemon=True).start()

    def disable_torque(self):
        self.io.set_mode({self.id: 0})
        self.io.disable_torque([self.id])

    def enable_torque(self):
        self.io.enable_torque([self.id])
        self.io.set_mode({self.id: 2})


    def update(self):
        while True:
            self.present_position = self.io.get_present_position([self.id])[0]
            error = self.goal_position - self.present_position

            pwm = self.kp * error
            # pwm *= 10
            pwm = np.int16(pwm)

            pwm_magnitude = abs(pwm)
            if pwm_magnitude >= 2**10:
                pwm_magnitude = (2**10) - 1

            direction_bit = 1 if pwm >= 0 else 0

            goal_time = (direction_bit << 10) | pwm_magnitude

            self.io.set_goal_time({self.id: goal_time})

            time.sleep(1 / self.control_freq)


motor = FeetechPWMControl()

s = time.time()
while True:

    target = 20 * np.sin(2 * np.pi * 0.5 * time.time())
    motor.goal_position = target

    if time.time() - s > 3 and time.time() - s < 6:
        motor.disable_torque()
        print("disbale")

    if time.time() - s > 6:
        motor.enable_torque()
        print("enable")
    time.sleep(1 / 60)


present_positions = []
goal_positions = []
present_loads = []
present_currents = []
present_speeds = []
times = []

motor.goal_position = 90

log_start = time.time()
s = time.time()
while time.time() - s < 2:
    present_positions.append(motor.io.get_present_position([motor.id])[0])
    goal_positions.append(motor.goal_position)
    present_loads.append(motor.io.get_present_load([motor.id])[0])
    present_currents.append(motor.io.get_present_current([motor.id])[0])
    present_speeds.append(motor.io.get_present_speed([motor.id])[0])
    times.append(time.time() - log_start)

motor.goal_position = -90
s = time.time()
while time.time() - s < 2:
    present_positions.append(motor.io.get_present_position([motor.id])[0])
    goal_positions.append(motor.goal_position)
    present_loads.append(motor.io.get_present_load([motor.id])[0])
    present_currents.append(motor.io.get_present_current([motor.id])[0])
    present_speeds.append(motor.io.get_present_speed([motor.id])[0])
    times.append(time.time() - log_start)
motor.goal_position = 90

s = time.time()
while time.time() - s < 2:
    present_positions.append(motor.io.get_present_position([motor.id])[0])
    goal_positions.append(motor.goal_position)
    present_loads.append(motor.io.get_present_load([motor.id])[0])
    present_currents.append(motor.io.get_present_current([motor.id])[0])
    present_speeds.append(motor.io.get_present_speed([motor.id])[0])
    times.append(time.time() - log_start)


data = {
    "present_positions": present_positions,
    "goal_positions": goal_positions,
    "present_loads": present_loads,
    "present_currents": present_currents,
    "present_speeds": present_speeds,
    "times": times,
}

pickle.dump(data, open("data_pwm_control.pkl", "wb"))

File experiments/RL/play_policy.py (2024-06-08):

import argparse
import time
from glob import glob

import gymnasium as gym
import mujoco
import mujoco.viewer
import numpy as np
from gymnasium.envs.registration import register
from stable_baselines3 import PPO, SAC

from mini_bdx.utils.mujoco_utils import check_contact


def get_observation(data, left_contact, right_contact):

    position = (
        data.qpos.flat.copy()
    )  # position/rotation of trunk + position of all joints
    velocity = (
        data.qvel.flat.copy()
    )  # positional/angular velocity of trunk +  of all joints

    obs = np.concatenate(
        [
            position,
            velocity,
            [left_contact, right_contact],
        ]
    )
    # print("OBS SIZE", len(obs))
    return obs


def key_callback(keycode):
    pass


def get_model_from_dir(path_to_model):

    if not path_to_model.endswith(".zip"):
        models_paths = glob(path_to_model + "/*.zip")
        latest_model_id = 0
        latest_model_path = None
        for model_path in models_paths:
            model_id = model_path.split("/")[-1][: -len(".zip")].split("_")[-1]
            if int(model_id) > latest_model_id:
                latest_model_id = int(model_id)
                latest_model_path = model_path

        if latest_model_path is None:
            print("No models found in directory: ", path_to_model)
            return
    else:
        latest_model_path = path_to_model

    return latest_model_path


def get_feet_contact(data, model):
    right_contact = check_contact(data, model, "foot_module", "floor")
    left_contact = check_contact(data, model, "foot_module_2", "floor")
    return right_contact, left_contact


def play(env, path_to_model):
    model_path = get_model_from_dir(path_to_model)

    model = mujoco.MjModel.from_xml_path("../../mini_bdx/robots/bdx/scene.xml")
    data = mujoco.MjData(model)

    left_contact = False
    right_contact = False

    viewer = mujoco.viewer.launch_passive(model, data, key_callback=key_callback)

    # nn_model = SAC.load(model_path, env)

    nn_model = PPO("MlpPolicy", env)
    nn_model.policy.load(model_path)

    try:
        while True:

            right_contact, left_contact = get_feet_contact(data, model)
            obs = get_observation(
                data,
                left_contact,
                right_contact,
            )
            action, _ = nn_model.predict(obs)
            data.ctrl[:] = action

            mujoco.mj_step(model, data)
            viewer.sync()
            time.sleep(model.opt.timestep / 2.5)

    except KeyboardInterrupt:
        viewer.close()

    viewer.close()


if __name__ == "__main__":

    parser = argparse.ArgumentParser(description="Test model")
    parser.add_argument(
        "-p",
        "--path",
        metavar="path_to_model",
        help="Path to the model. If directory, will use the latest model.",
    )
    parser.add_argument("-a", "--algo", default="SAC")
    args = parser.parse_args()

    register(id="BDX_env", entry_point="env_humanoid:BDXEnv")
    env = gym.make("BDX_env", render_mode=None)
    play(env, path_to_model=args.path)

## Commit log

2024-05-19 updating xmlsé
    [example_robot.xml]
2024-05-19 starting walk training
    [example_robot.xml]
2024-05-20 velocity reward in the right direction this time :)
2024-06-11 stl to print
    [dummy_horn.stl, foot.stl, foot_contact.stl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]
2024-07-14 reordered joints
2024-07-15 amp stuff
    [robot.xml]
2024-07-16 catastrophic inversion of the legs from the beggining in actuators ...
    [robot.xml, scene_test.xml]
2024-07-16 sim2sim working !
    [robot.xml]
2024-07-21 cleaning stuff
    [robot.xml, scene_test.xml]
2024-09-16 cleaning up
    [robot.xml]
2024-12-09 replay imu data script
2025-01-06 placo walk open loop
    [body_back.stl, body_front.stl, body_middle_bottom.stl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]
2025-01-07 updated urdf and mjcf
    [antenna.stl, battery_pack_lid.stl, bno055.stl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]
2025-01-10 configure motors works
2025-01-11 configure motors
2025-01-15 new urdf and mjcf
    [bms.stl, bno055.stl, body_back.stl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]
